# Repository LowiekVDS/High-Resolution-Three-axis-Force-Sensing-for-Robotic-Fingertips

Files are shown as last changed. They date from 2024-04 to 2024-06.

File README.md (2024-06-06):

# High Resolution Three-axis Force Sensing for Robotic Fingertips

This is the GitHub repository related to my masters disseration. It contains the CAD and software used

## Overview
- CAD: contains mechanical CAD data from Siemens NX and .obj files
- data: some .csv files recored using the procedure described in the dissertation
- electrical: EasyEDA files
- models: trained models for my prototype
- notebooks: contains code for calibration,readout, plotting and model creation
- plotjuggler: preset for PlotJuggler stuff
- sensor-readout: A Platform IO project for the microcontroller reading out the sensor array

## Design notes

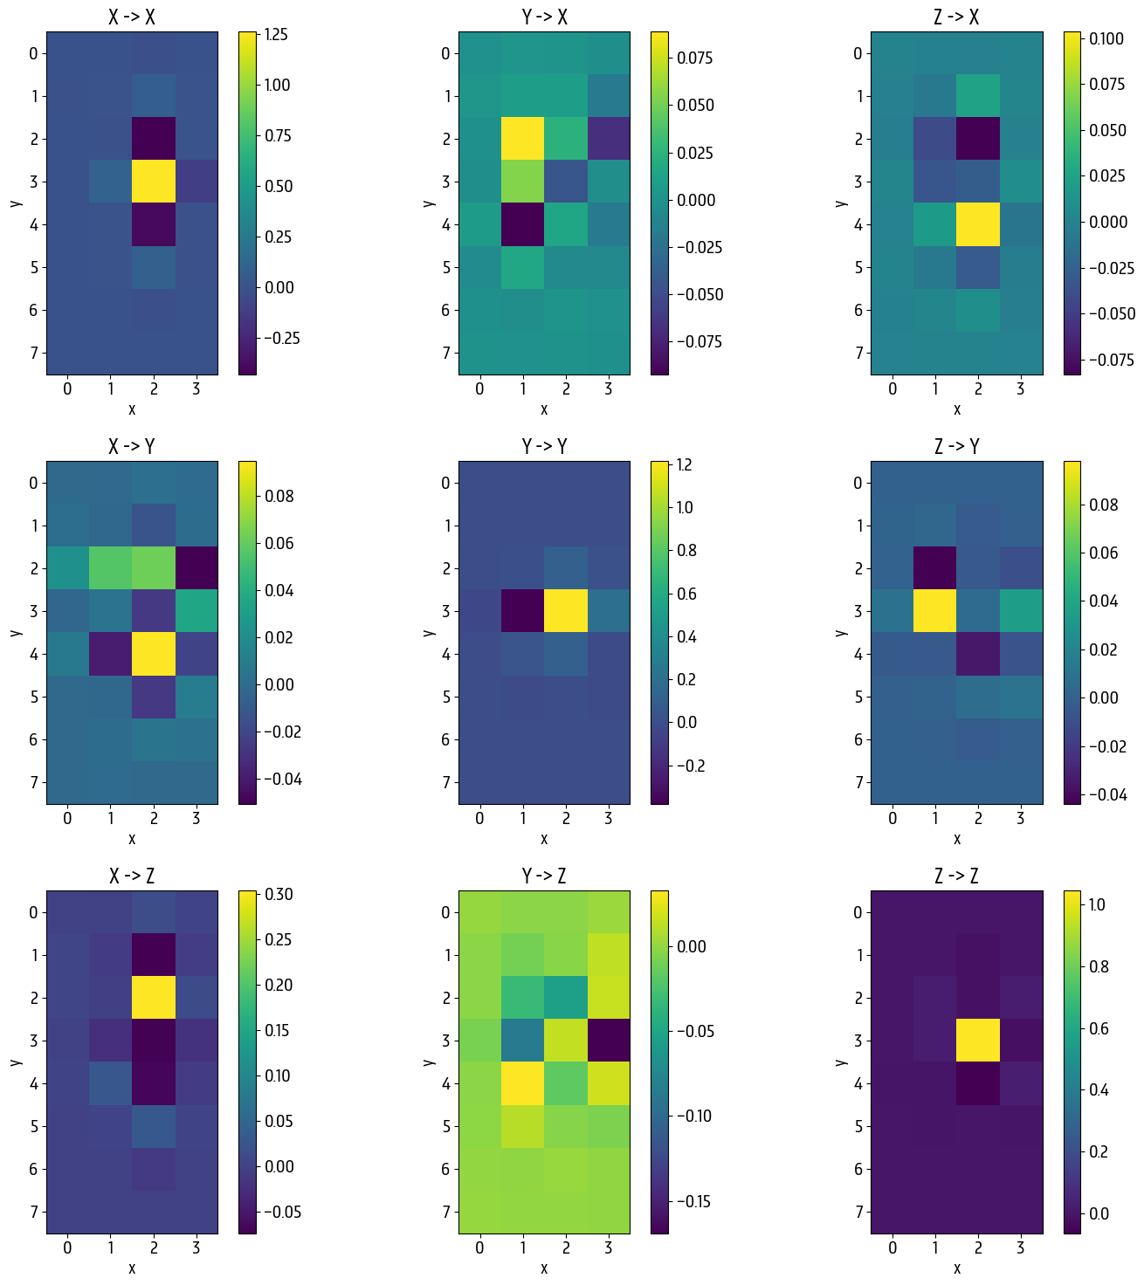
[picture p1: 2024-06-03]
notebooks/plots/c4_stageII_matrices.png

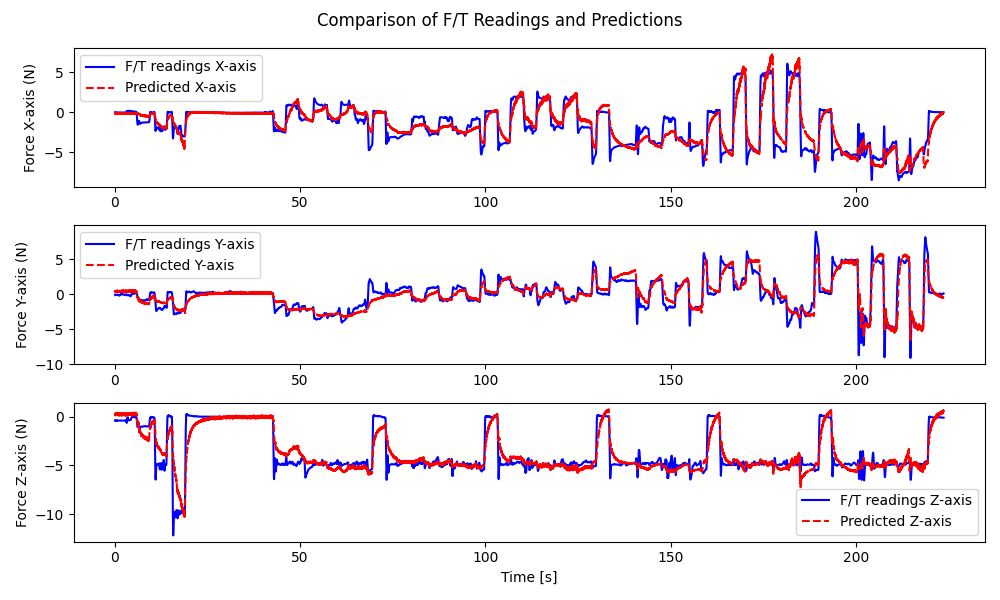
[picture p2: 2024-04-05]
notebooks/prediction_comparison_plot.png

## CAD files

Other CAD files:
CAD/4x8/Case/mold_top.obj
CAD/4x8/Domes/dummy_domes.obj
CAD/4x8/PCB/3D_4x8_2024-04-07.step
CAD/auto_calibration/2x2/bovenkant_tafel.obj
CAD/auto_calibration/4x8/table_mount.obj
CAD/auto_calibration/probe.obj
CAD/manual_calibration/onderkant.obj
CAD/reverse_calibration/houder.obj
CAD/4x8/Case/top.obj
CAD/4x8/Domes/4_5_x1-001.obj
CAD/auto_calibration/2x2/onderkant.obj
CAD/manual_calibration/bovenkant.obj
CAD/reverse_calibration/probe.obj
CAD/4x8/Case/bottom.obj
CAD/manual_calibration/pressure_applyer.obj
CAD/2x2/dome_1.5mm_v2/dome_1.5mm.prt
CAD/2x2/dome_1.5mm_v2/dome_1.5mm_filled.prt
CAD/2x2/dome_1.5mm_v2/dome_1.5mm_filled_v2.prt
CAD/2x2/dome_1.5mm_v2/mold.prt
CAD/2x2/dome_1.5mm_v2/pressure_applyer.prt
CAD/2x2/dome_1mm_v2/dome_1mm.prt
CAD/2x2/dome_1mm_v2/dome_1mm_filled.prt
CAD/2x2/dome_1mm_v2/dome_1mm_filled_v2.prt
CAD/2x2/dome_2mm_v2/dome_2mm.prt
CAD/2x2/dome_2mm_v2/dome_2mm_filled.prt
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

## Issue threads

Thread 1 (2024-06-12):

Questions about the model of circuit board components

Newhandsomeman, 2024-06-12:
We use the BOM table exported by your file in Jialichuang EDA, some devices do not have a specific model, such as the patch resistor encapsulated as R0603 （C9900014833）has no resistance information.Could you please add certain information？

LowiekVDS, 2024-06-17:
Hello! Those resistors are pull-up resistors for the I2C lines. A value of 10kOhm should suffice. Note that depending on which microcontroller you are using, the main I2C bus (SDA, SCL) might also require (external) pull-ups.

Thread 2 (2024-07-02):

Questions about the software environment

Newhandsomeman, 2024-07-02:
I am having some problems configuring the software environment.
Seeing that you are using python language and raspberry pi for development, is the programming software configured in pycharm or thonny or vs code?From your file structure it looks like you are using notebook and vs code, but I am not quite sure how this aspect is configured.
In your code, the notebook part should be using jupyter, is this part done online or offline for training (connecting sensors to get data online)?
Is the sensorreadout part based on vscode configuring the micro-python environment to control the raspberry pi? I would like you to give some explanation on this part. I didn't find any tutorials on vscode configuration for controlling raspberry pi with python language.
Thank you!

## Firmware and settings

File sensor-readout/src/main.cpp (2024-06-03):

#include "SensorArray.h"
#include <math.h>
#include <Wire.h>
#include "taxels.h"

// EDITABLE

// #define DEBUG 1

#define SEND_FORCE_PREDICTIONS true
#define ENABLE_STAGE_II true

#define BAUD_RATE 400000
#define MLX_OSR MLX90393_OSR_2
#define MLX_DIG_FILT MLX90393_FILTER_1
#define START_BYTE 0xAA
#define MUX_ADDR 0x77
#define USE_MUX 1

#define HEADER_SIZE 1
#define TAIL_SIZE 0
#define SUBFRAME_SIZE 6
#define I2C_SPEED 400000 // in kHz
#define EXTRA_DELAY 0
#define ANGLE 1.6025613
#define DEBIAS_WINDOW 100

// Readout is done in this order.
// Done so that a mapping can be made between different physical and logical layouts
// Can also be used to have different readout strategies

#define NR_OF_SENSORS 8 * 4

// Left to right
uint8_t addressing_left_to_right[NR_OF_SENSORS] =
    {

        0x3C,
        0x3D,
        0x3E,
        0x3F,
        0x4C,
        0x4D,
        0x4E,
        0x4F,
        0x2C,
        0x2D,
        0x2E,
        0x2F,
        0x1C,
        0x1D,
        0x1E,
        0x1F,
        0x0C,
        0x0D,
        0x0E,
        0x0F,
        0x5C,
        0x5D,
        0x5E,
        0x5F,
        0x6C,
        0x6D,
        0x6E,
        0x6F,
        0x7C,
        0x7D,
        0x7E,
        0x7F,
};

//! Choose mapping here
uint8_t *sensor_addresses = addressing_left_to_right;

// END EDITABLE

Adafruit_MLX90393 sensors[NR_OF_SENSORS];
SensorArray sensorArray(I2C_SPEED, sensors, MUX_ADDR);

uint16_t x[NR_OF_SENSORS], y[NR_OF_SENSORS], z[NR_OF_SENSORS];
float prev_x[NR_OF_SENSORS], prev_y[NR_OF_SENSORS], prev_z[NR_OF_SENSORS];
int x_cycle[NR_OF_SENSORS], y_cycle[NR_OF_SENSORS], z_cycle[NR_OF_SENSORS];
float x_bias[NR_OF_SENSORS], y_bias[NR_OF_SENSORS], z_bias[NR_OF_SENSORS];

long conversion_time_us, comm_time_us, idle_time_us = 0;

uint8_t id = 0;
bool started = false;

bool is_first = true;

uint8_t debiasing_counter = 0;

void setup()
{
    Wire.begin();

    // Set up serial communication
    Serial.begin(BAUD_RATE);

    /* Wait for serial on USB platforms. */
    while (!Serial)
    {
        delay(10);
    }

    // Setup sensor array
    bool success = sensorArray.addSensors(sensor_addresses, NR_OF_SENSORS);

    if (!success)
    {
        // Note: why doesn't Serial have a printf :(
        Serial.print("[FATAL]> Something went wrong while adding sensors");

        while (1)
            ;
    }

    for (int i = 0; i < sensorArray.getNumberOfSensors(); i++)
    {

        auto sensor = sensorArray.getSensor(i);

        // Set gain and resolution

        sensor->setGain(MLX90393_GAIN_1X);
        sensor->setResolution(MLX90393_X, MLX90393_RES_16);
        sensor->setResolution(MLX90393_Y, MLX90393_RES_16);
        sensor->setResolution(MLX90393_Z, MLX90393_RES_16);

        // Set oversampling
        sensor->setOversampling(MLX_OSR);

        // Enable temperature compensation
        sensor->setTemperatureCompensation(true);

        // Set digital filtering
        sensor->setFilter(MLX_DIG_FILT);
    }

    // Calculate the different timings
    conversion_time_us = ceil(1000 * (0.5 + 3 * 0.063 * pow(2.0, MLX_OSR) * (2 + pow(2.0, MLX_DIG_FILT)) + 1)); // + 1 for good measure
    comm_time_us = 8 * 1000000 * (HEADER_SIZE + TAIL_SIZE + NR_OF_SENSORS * SUBFRAME_SIZE) / BAUD_RATE;
    idle_time_us = conversion_time_us - NR_OF_SENSORS * 40000000 / I2C_SPEED - comm_time_us;

    Serial.println("Conversion time: " + String(conversion_time_us) + " us");
    Serial.println("Communication time: " + String(comm_time_us) + " us");
    Serial.println("Idle time: " + String(idle_time_us) + " us");

    if (idle_time_us < 0)
    {
        Serial.println("[WARNING]> Idle wait time is negative, which means the system is underutilized or constrained by Serial speed. Please reconfigure");
        idle_time_us = 0.0;
    }

    idle_time_us += EXTRA_DELAY;
}

uint16_t convert(float fval, float min, float max)
{
    if (fval < min)
        return (0);
    if (fval > max)
        return (UINT16_MAX);
    return (lrintf((fval - min) / (max - min) * UINT16_MAX));
}

void loop()
{
    // Read loop. First step is to start measurements
    for (uint8_t i = 0; i < sensorArray.getNumberOfSensors(); i++)
    {
        if (!sensorArray.getSensor(i)->startSingleMeasurement())
        {
            Serial.println("[WARNING]> Sensor measurement failed");
        }
    }

    // Now send previous data
    if (started)
    {

#ifndef DEBUG

        if (!SEND_FORCE_PREDICTIONS)
        {
            Serial.write(START_BYTE);

            for (uint8_t i = 0; i < NR_OF_SENSORS; i++)
            {
                Serial.write((x[i] >> 8) & 0xFF);
                Serial.write(x[i] & 0xFF);

                Serial.write((y[i] >> 8) & 0xFF);
                Serial.write(y[i] & 0xFF);

                Serial.write((z[i] >> 8) & 0xFF);
                Serial.write(z[i] & 0xFF);
            }
        }
        else
        {

            float feature_input_stage_II[3 * NR_OF_SENSORS];

            for (uint8_t i = 0; i < NR_OF_SENSORS; i++)
            {

                // Conversion based on sensor settings (to uT)
                float x_f = ~x[i];
                float y_f = ~y[i];
                float z_f = ~z[i];

                // Unwrapping
                if (!is_first)
                {
                    if (abs(x_f - prev_x[i]) > pow(2, 15))
                    {
                        x_cycle[i] += x_f < prev_x[i] ? 1 : -1;
                    }
                    if (abs(y_f - prev_y[i]) > pow(2, 15))
                    {
                        y_cycle[i] += y_f < prev_y[i] ? 1 : -1;
                    }
                    if (abs(z_f - prev_z[i]) > pow(2, 15))
                    {
                        z_cycle[i] += z_f < prev_z[i] ? 1 : -1;
                    }
                }

                prev_x[i] = x_f;
                prev_y[i] = y_f;
                prev_z[i] = z_f;

                x_f = x_f + 65536 + x_cycle[i] * 65536;
                y_f = y_f + 65536 + y_cycle[i] * 65536;
                z_f = z_f + 65536 + z_cycle[i] * 65536;

                x_f = x_f * 0.150;
                y_f = y_f * 0.150;
                z_f = z_f * 0.242;

                // Global feature transformation
                float x_temp = x_f;
                float y_temp = y_f;

                x_f = x_temp * cos(ANGLE) - y_temp * sin(ANGLE);
                y_f = x_temp * sin(ANGLE) + y_temp * cos(ANGLE);

                // Local feature transformation
                z_f = (float)1.0 / z_f;

                // Debiasing
                if (debiasing_counter < DEBIAS_WINDOW)
                {
                    x_bias[i] += x_f;
                    y_bias[i] += y_f;
                    z_bias[i] += z_f;

                    x_f = 0;
                    y_f = 0;
                    z_f = 0;
                }
                else
                {

                    x_f -= x_bias[i] / DEBIAS_WINDOW;
                    y_f -= y_bias[i] / DEBIAS_WINDOW;
                    z_f -= z_bias[i] / DEBIAS_WINDOW;
                }

                // Make polynomial features
                float polynomials[20];
                generate_polynomial_features(x_f, y_f, z_f, polynomials);

                // Apply stage I
                apply_model(coef_pointers[i], polynomials, feature_input_stage_II + 3 * i);
            }

            if (debiasing_counter <= DEBIAS_WINDOW)
                debiasing_counter++;

            is_first = false;

            float feature_output_stage_II[3 * NR_OF_SENSORS];

            if (ENABLE_STAGE_II)
            {
                apply_stage_II(feature_input_stage_II, feature_output_stage_II);
            }

            if (debiasing_counter <= DEBIAS_WINDOW)
            {
                delayMicroseconds(comm_time_us);
                return;
            }

            // Output stage. Convert to

            float *to_send = ENABLE_STAGE_II ? feature_output_stage_II : feature_input_stage_II;

            // Convert to 2 bytes and send
            Serial.write(START_BYTE);
            for (uint8_t i = 0; i < 3 * NR_OF_SENSORS; i++)
            {

                uint16_t val;

                if (i % 3 == 2)
                {
                    //  Serial.println(to_send[i]);
                    val = convert(to_send[i], -30.0, 10.0);
                    // Serial.println(val);
                }
                else
                    val = convert(to_send[i], -10.0, 10.0);

                // if (i == 2) {
                //     Serial.println(val);
                // }

                Serial.write((val >> 8) & 0xFF);
                Serial.write(val & 0xFF);
            }
        }
#endif
    }
    else
    {
        delayMicroseconds(comm_time_us);
    }

    delayMicroseconds(idle_time_us);

    // Read measurements data
    for (uint8_t i = 0; i < sensorArray.getNumberOfSensors(); i++)
    {

#ifndef DEBUG
        if (!sensorArray.getSensor(i)->readRawMeasurement(x + i, y + i, z + i))
        {
            Serial.print("Something went wrong in sensor ");
            Serial.println(i);
        }
#else
        float x, y, z;
        if (!sensorArray.getSensor(i)->readMeasurement(&x, &y, &z))
        {
            Serial.println("ERROR");
            continue;
        }
        Serial.print("S");
        Serial.print(i);
        Serial.print(" ( ");
        Serial.print(x);
        Serial.print(" ; ");
        Serial.print(y);
        Serial.print(" ; ");
        Serial.print(z);
        Serial.print(" ) \n");

#endif
    }

    started = true;
    id++;
}

// --------------------------------------
// i2c_scanner
//
// Version 1
//    This program (or code that looks like it)
//    can be found in many places.
//    For example on the Arduino.cc forum.
//    The original author is not know.
// Version 2, Juni 2012, Using Arduino 1.0.1
//     Adapted to be as simple as possible by Arduino.cc user Krodal
// Version 3, Feb 26  2013
//    V3 by louarnold
// Version 4, March 3, 2013, Using Arduino 1.0.3
//    by Arduino.cc user Krodal.
//    Changes by louarnold removed.
//    Scanning addresses changed from 0...127 to 1...119,
//    according to the i2c scanner by Nick Gammon
//    https://www.gammon.com.au/forum/?id=10896
// Version 5, March 28, 2013
//    As version 4, but address scans now to 127.
//    A sensor seems to use address 120.
// Version 6, November 27, 2015.
//    Added waiting for the Leonardo serial communication.
//
//
// This sketch tests the standard 7-bit addresses
// Devices with higher bit address might not be seen properly.
//

// #include <Wire.h>

// void setup()
// {
//   Wire.begin();

//   Serial.begin(9600);
//   while (!Serial);             // Leonardo: wait for serial monitor
//   Serial.println("\nI2C Scanner");

//   Wire.beginTransmission(0x77);
//   Wire.write(0x01 << 3);
//   if (Wire.endTransmission() == false)
//   {
//     Serial.println("Success");
//   }
// }

// void loop()
// {
//   byte error, address;
//   int nDevices;

//   Serial.println("Scanning...");

//   nDevices = 0;
//   for(address = 1; address < 127; address++ )
//   {
//     // The i2c_scanner uses the return value of
//     // the Write.endTransmisstion to see if
//     // a device did acknowledge to the address.
//     Wire.beginTransmission(address);
//     error = Wire.endTransmission();

//     if (error == 0)
//     {
//       Serial.print("I2C device found at address 0x");
//       if (address<16)
//         Serial.print("0");
//       Serial.print(address,HEX);
//       Serial.println("  !");

//       nDevices++;
//     }
//     else if (error==4)
//     {
//       Serial.print("Unknown error at address 0x");
//       if (address<16)
//         Serial.print("0");
//       Serial.println(address,HEX);
//     }
//   }
//   if (nDevices == 0)
//     Serial.println("No I2C devices found\n");
//   else
//     Serial.println("done\n");

//   delay(5000);           // wait 5 seconds for next scan
// }

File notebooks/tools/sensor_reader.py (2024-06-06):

import os
import time
import json
import csv
import os
import time
import json
import socket
import serial
from .mlx import *
import multiprocessing
import numpy as np
import cv2
import time

#
#
# START EDIT PARAMETERS
#
#

GAIN = 7 # Gain setting (same as firmware)
RESOLUTION = 0 # Resolution setting (same as firmware)
BAUD = 115200 # Baud rate
COM = '/dev/ttyACM0' # Serial port
ENABLE_WS = True # Enable WebSocket server. Disable if not using websocket. Script will crash otherwise.
NR_OF_SENSORS = 32 # Number of sensors
TEMP_COMP = True

#
#
# END EDIT PARAMETERS
#
#

def plot_colormap(queue):
    
    is_first = True
    zero_data = [np.zeros((8, 4)), np.zeros((8, 4)), np.zeros((8, 4))]
  
    while True:
        all_data = queue.get()
        if all_data is None:
            break
        
        components = ['X', 'Y', 'Z']
        for i in range(3):
            
            data = all_data[i * 32 : (i + 1) * 32]
            
            # Reshape the 1D array into a 2D array (4x8)
            data_matrix = np.reshape(data, (8, 4)) - zero_data[i]

            if is_first:
                zero_data[i] = data_matrix
                continue
            
            data_matrix = np.abs(data_matrix)

            # Scale the values to 0-255 for better visualization
            val_range = np.max(data_matrix)
            
            
            data_matrix = ((data_matrix) / val_range * 255).astype(np.uint8)

            # Create a colormap image using OpenCV
            colormap = cv2.applyColorMap(data_matrix, cv2.COLORMAP_BONE)

            scaled_colormap = cv2.resize(colormap, (400, 800), interpolation=cv2.INTER_NEAREST)  # Adjust the size as needed

            # Display the resized colormap image
            cv2.imshow('Map ' + components[i], scaled_colormap)
        
        if is_first:
            is_first = False
        
        cv2.waitKey(1)


ser = serial.Serial(COM, BAUD) 
    

def read_and_publish_sensor_sync(name, que, visualize=True):

    if visualize:
        queue = multiprocessing.Queue()
        process = multiprocessing.Process(target=plot_colormap, args=(queue,))
        process.start()
        
    level = 0
    
    prev_x = [0] * NR_OF_SENSORS
    prev_y = [0] * NR_OF_SENSORS
    prev_z = [0] * NR_OF_SENSORS
    
    cycle_x = [0] * NR_OF_SENSORS
    cycle_y = [0] * NR_OF_SENSORS
    cycle_z = [0] * NR_OF_SENSORS
    
    is_first = True

    # Define the UDP server address and port
    udp_server_address = ('localhost', 9870)

    # Create a UDP socket
    udp_socket = socket.socket(socket.AF_INET, socket.SOCK_DGRAM)

    with open( os.path.join(os.path.dirname(os.path.realpath(__file__)), f'../../data/raw/sensor/table_calibration/{name}.csv'), 'w', newline='') as csvfile:

        csv_writer = csv.writer(csvfile)
        header_row = ["t_wall [s]", "level_sensor []"]
        for i in range(NR_OF_SENSORS):
            header_row.append(f"X{i} [uT]")
            header_row.append(f"Y{i} [uT]")
            header_row.append(f"Z{i} [uT]")
            
        csv_writer.writerow(header_row)
        
        is_running = True
        
        if not ser.is_open:
            ser.open()
        
        while is_running:
        
            if not que.empty():
                cmd = que.get()
                
                if cmd[0] == "stop":
                    is_running = False
                    ser.read(1)
                    continue
                elif cmd[0] == "set_level":
                    level = cmd[1]           
        
            data = ser.read(1)
            if data == b'\xAA':
                data_bytes = ser.read(6 * NR_OF_SENSORS)
                row = {"t": time.time(), "level_sensor": level}

                for i in range(NR_OF_SENSORS):
                    x = ~ ( (data_bytes[i * 3 * 2] << 8) + data_bytes[i * 3 * 2 + 1] )
                    y = ~ ( (data_bytes[i * 3 * 2 + 2] << 8) + data_bytes[i * 3 * 2 + 3] )
                    z = ~ ( (data_bytes[i * 3 * 2 + 4] << 8) + data_bytes[i * 3 * 2 + 5] )

                    if not is_first:
                        
                        # Check for large jumps and correct them
                        if abs(x - prev_x[i]) > 2 ** 15:
                            cycle_x[i] += 1 if x < prev_x[i] else -1
                            
                        if abs(y - prev_y[i]) > 2 ** 15:
                            cycle_y[i] += 1 if y < prev_y[i] else -1
                        
                        if abs(z - prev_z[i]) > 2 ** 15:
                            cycle_z[i] += 1 if z < prev_z[i] else -1      
                    
                    prev_x[i] = x
                    prev_y[i] = y
                    prev_z[i] = z
                    
                    x += cycle_x[i] * 2 ** 16
                    y += cycle_y[i] * 2 ** 16
                    z += cycle_z[i] * 2 ** 16                    
                                            
                    is_first = False

                    x *= mlx90393_lsb_lookup[0][GAIN][RESOLUTION][0] 
                    y *= mlx90393_lsb_lookup[0][GAIN][RESOLUTION][0] 
                    z *= mlx90393_lsb_lookup[0][GAIN][RESOLUTION][1] 
                    
                    x += mlx90393_lsb_lookup[0][GAIN][RESOLUTION][0] * 2 ** 16
                    y += mlx90393_lsb_lookup[0][GAIN][RESOLUTION][0] * 2 ** 16
                    z += mlx90393_lsb_lookup[0][GAIN][RESOLUTION][1] * 2 ** 16

                    row[f"X{i}"] = x
                    row[f"Y{i}"] = y
                    row[f"Z{i}"] = z
 
                csvrow = [row["t"], row["level_sensor"]]
                
                for i in range(NR_OF_SENSORS):
                    csvrow.append(row[f"X{i}"])
                    csvrow.append(row[f"Y{i}"])
                    csvrow.append(row[f"Z{i}"])

                if visualize:
                    queue.put(np.array([row[f"X{i}"] for i in range(NR_OF_SENSORS)] + [row[f"Y{i}"] for i in range(NR_OF_SENSORS)] + [row[f"Z{i}"] for i in range(NR_OF_SENSORS)]))

                csv_writer.writerow(csvrow)
                json_data = json.dumps(row)
                udp_socket.sendto(json_data.encode(), udp_server_address)                

        udp_socket.close()
        ser.close()
        
        if visualize:
            queue.put(None)
            process.join()
        

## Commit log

2023-10-10 Added sensor readout demo exampl
2023-10-15 Added do_stop fix for platform
    [data.csv]
2023-10-15 Added websocket to python file
    [data.csv]
2023-11-15 added CAD
    [Sensor_PCB.prt, assembly.prt, bovenkant.prt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]
2023-12-18 Lots of data!
    [H1-s0-20231218-001.csv, H1-s0-20231218-002.csv, H1-s0-20231218-003.csv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]
2024-01-03 normal data
    [H1_2x2_sil50_2mm_20231116_172016.csv, H1_2x2_sil50_2mm_20231116_172017.csv, H1_2x2_sil50_3mm_20231116_172336.csv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]
2024-01-03 git lfs data
    [2F-85_20Sillicone_20Finger_20181108.STEP, 2F-85_20Sillicone_20Finger_20181108_step.prt, 2F85_Opened_20190924.STEP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]
2024-01-03 Added readme
    [H1_sensor0_air_20231116_171501.csv, k.csv, test.csv]
2024-02-09 Added ROS workspace
    [board.stl, fake_controllers.yaml, gripper_controller.yaml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]
2024-03-06 new data!
    [2x2_grid_normal.csv, 2x2_grid_normal_probe_06032024.csv, 2x2_grid_subsampling_x1_normal_probe_06032024.csv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]
2024-03-08 Weer data
    [2x2_grid_normal.csv, 2x2_grid_normal_probe_06032024.csv, 2x2_grid_subsampling_x1_08032024.csv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]
2024-03-20 data 3
    [2x2_grid_subsampling_validatie_2_20032024.csv, 2x2_grid_subsampling_validatie_3_20032024.csv]
2024-04-14 sensor readout works for 32 sensors
2024-04-17 new data of 4x8!
    [taxel0.csv, taxel1.csv, taxel10.csv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]
2024-05-22 spiral calib
    [sillicon_taxel0.csv, sillicon_taxel9.csv, spiral_taxel0.csv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]
